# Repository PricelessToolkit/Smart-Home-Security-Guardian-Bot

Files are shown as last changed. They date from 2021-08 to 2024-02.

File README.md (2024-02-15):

# HABot

### https://youtu.be/2BBThH_CpSE

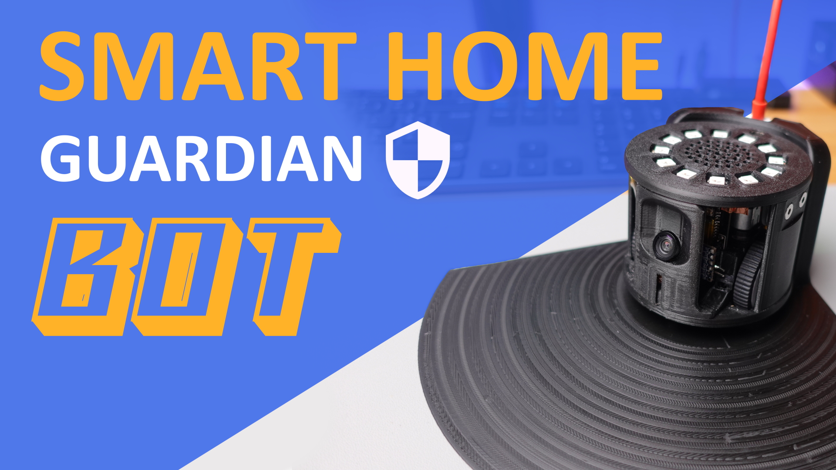
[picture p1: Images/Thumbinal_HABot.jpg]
habot (https://youtu.be/2BBThH_CpSE)


## Want to support me? Subscribe and like!

## Features

* 1: Tiny size
* 2: Wireless Charging
* 3: Voice Notifications
* 4: LED Indication
* 5: Build-in Motion sensor
* 6: Build-in Light level Sensor
* 7: MQTT Controls
* 8: Live Video stream

## Configuration Instructions
"Config_Arduino.txt" "Config_ESP32Cam.txt" "Config_Home_Assistant.txt"

## Connection diagram

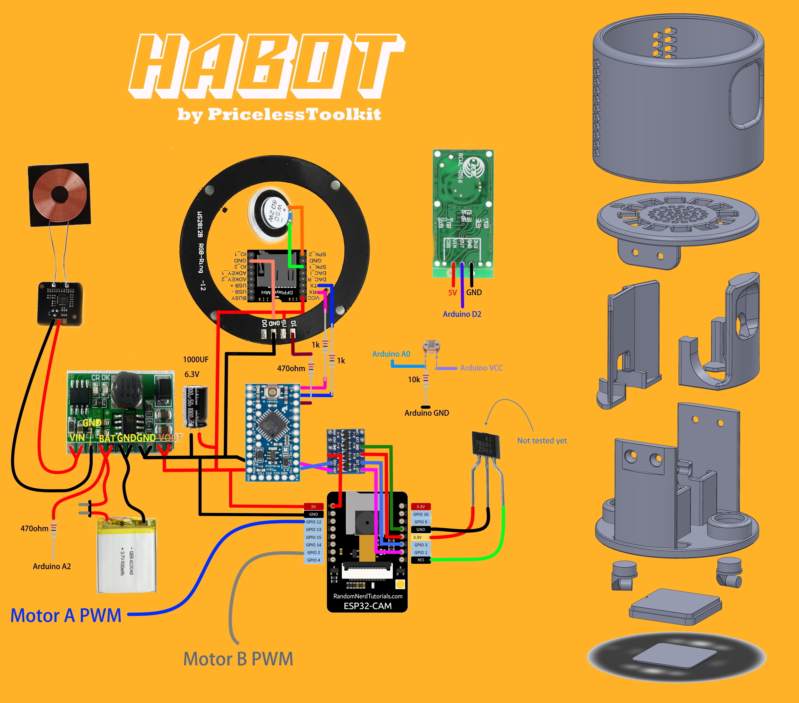
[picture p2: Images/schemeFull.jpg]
Connectiondiagram
[

## Part list

Arduino Pro Mini 5v
* 1: Speaker https://s.click.aliexpress.com/e/_AtpwE7
* 2: ESP32-CAM https://s.click.aliexpress.com/e/_AXyxo3
* 3: 160 degree OV2640 Camera https://s.click.aliexpress.com/e/_AlQi75
* 4: Wireless charger https://s.click.aliexpress.com/e/_AYQFs7
* 5: wireless charger receiver 2x2cm https://s.click.aliexpress.com/e/_API7jD
* 6: 2x Motor Single side 90deg size D https://s.click.aliexpress.com/e/_AmKxZ5
* 7: 2x Wheel https://s.click.aliexpress.com/e/_DlZWzxj
* 8: DF Player https://s.click.aliexpress.com/e/_9IVHIR
* 9: RCWL 0516 Microwave Radar Sensor https://s.click.aliexpress.com/e/_ADjEIj
* 10: LDR Light Dependent Resistor 5506 https://s.click.aliexpress.com/e/_A7hNt9
* 11: 2x chipset servo SG90  https://s.click.aliexpress.com/e/_9Qcnwr   or 2x "Servo controller tested working !" https://s.click.aliexpress.com/e/_9G644J
* 12: Charging board https://www.aliexpress.com/item/32816254080.html?spm=a2g0s.9042311.0.0.27424c4dwZKibe
* 13: Led WS2812 12xLED 5050 RGB https://s.click.aliexpress.com/e/_DBnUIml
* 14: Level SHifter https://s.click.aliexpress.com/e/_AScY1h
* 15: 1x Voltage supervisor https://s.click.aliexpress.com/e/_9HgdKX
* 16: Battery WITH PROTECTION !!!! https://s.click.aliexpress.com/e/_AXWZJD
* 17: 2 x Ball-bearing 10X15X4 mm https://s.click.aliexpress.com/e/_9G0KCn
* 18: 2 x Ball-bearing 5x10x4 https://s.click.aliexpress.com/e/_AD9iDh
* 19: 30 AWG Silicon !!! wires https://s.click.aliexpress.com/e/_Alra0B
* 20: Capacitor 6.3v 1000uf https://s.click.aliexpress.com/e/_An0GSx
* 21: Aluminum or copper self-adhesive tape
* 22: Resistors: 2 x 1K, 2 x 470R, 1x 10K
* 23: Resistor 2x SMD 0806 2.7k

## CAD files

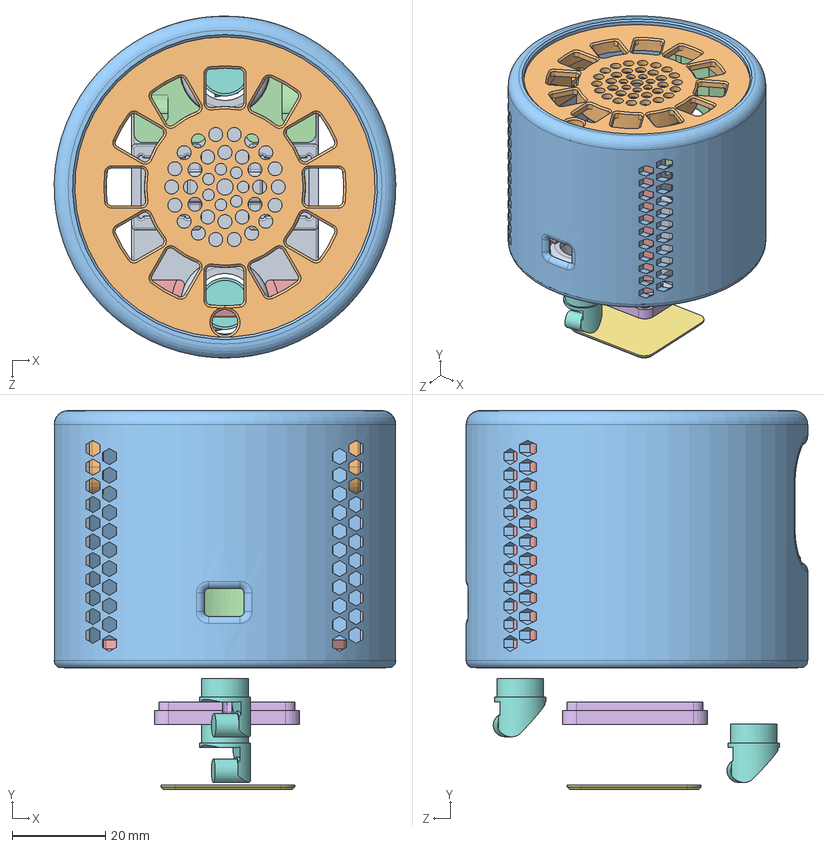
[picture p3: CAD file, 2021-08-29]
3D/SolidWorks/Assem1.SLDASM
73.2 x 81.2 x 73.2 mm
Base
Top
kash
camera holder
ArduinoHolder
WirelessChargingStand
WirelessChargingStandEndPart
bearing x 2

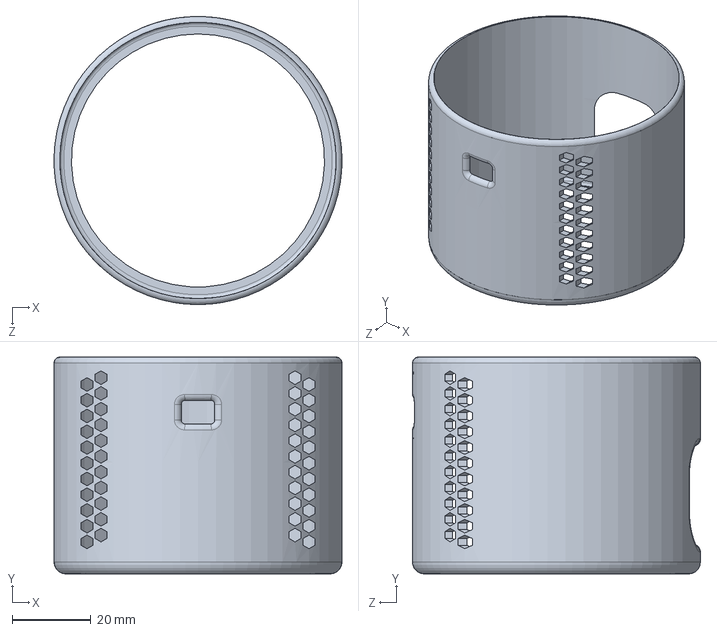
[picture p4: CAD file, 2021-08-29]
3D/SolidWorks/Cover.SLDPRT
73.2 x 55.1 x 73.2 mm

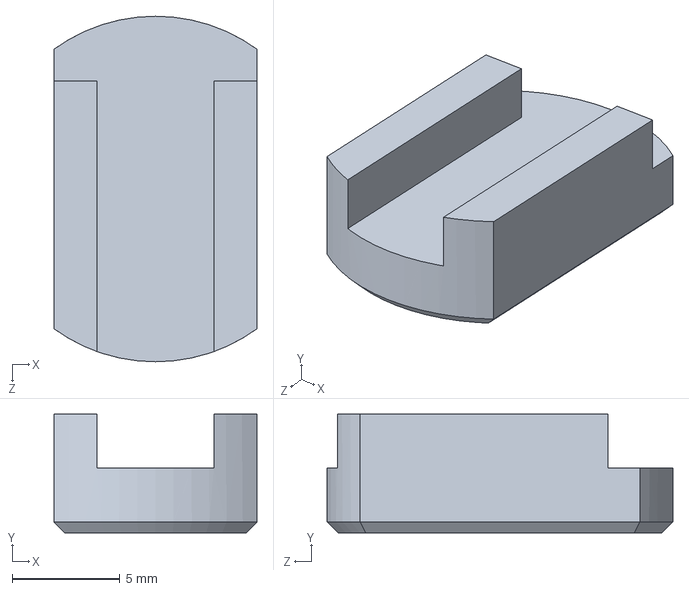
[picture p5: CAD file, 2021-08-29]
3D/SolidWorks/jumper holder.SLDPRT
9.40 x 5.50 x 16.0 mm

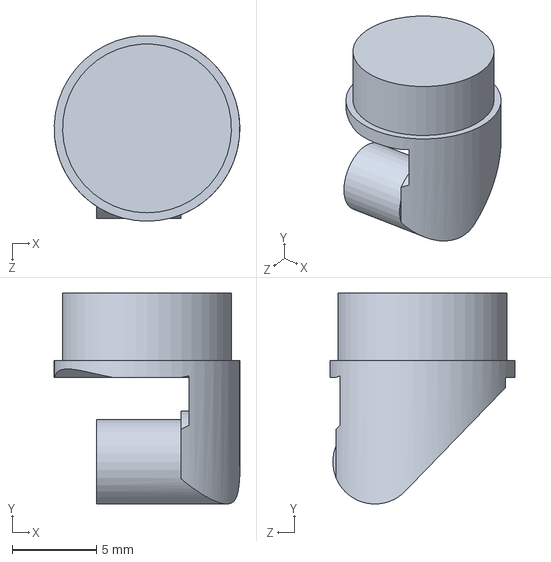
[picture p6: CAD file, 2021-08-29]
3D/SolidWorks/bearing.SLDPRT
11.0 x 12.5 x 11.0 mm

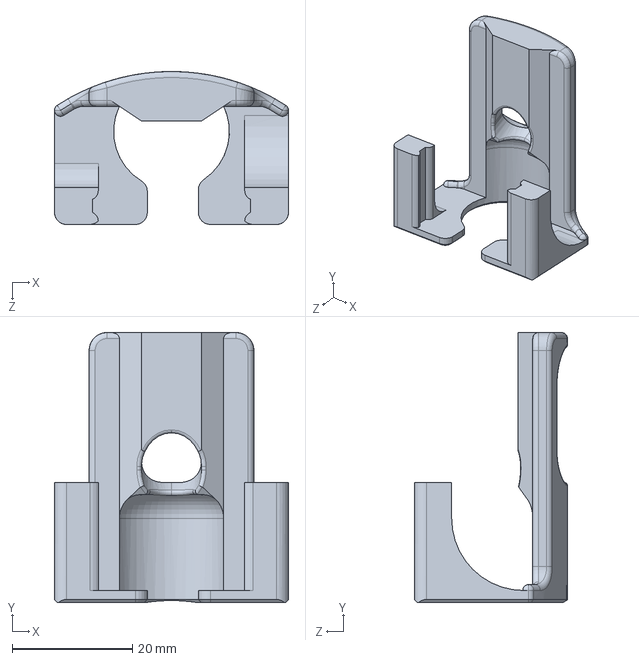
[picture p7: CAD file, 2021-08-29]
3D/SolidWorks/camera holder.SLDPRT
39.0 x 45.0 x 25.5 mm

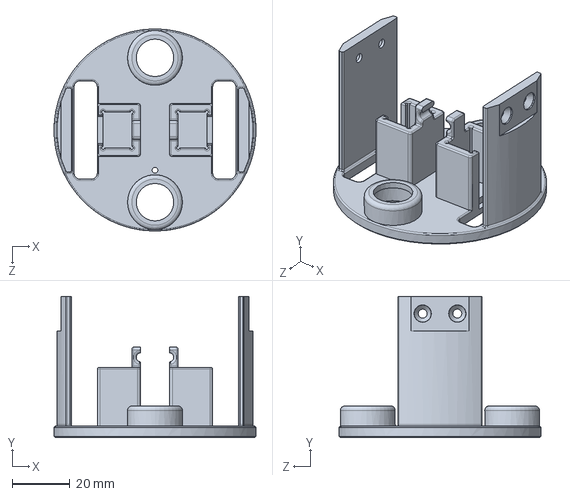
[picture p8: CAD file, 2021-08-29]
3D/SolidWorks/Base.SLDPRT
70.0 x 49.0 x 70.0 mm

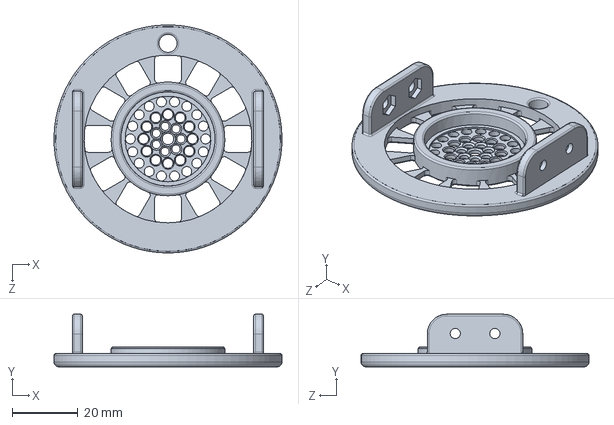
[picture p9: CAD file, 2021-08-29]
3D/SolidWorks/Top.SLDPRT
69.2 x 16.0 x 69.2 mm

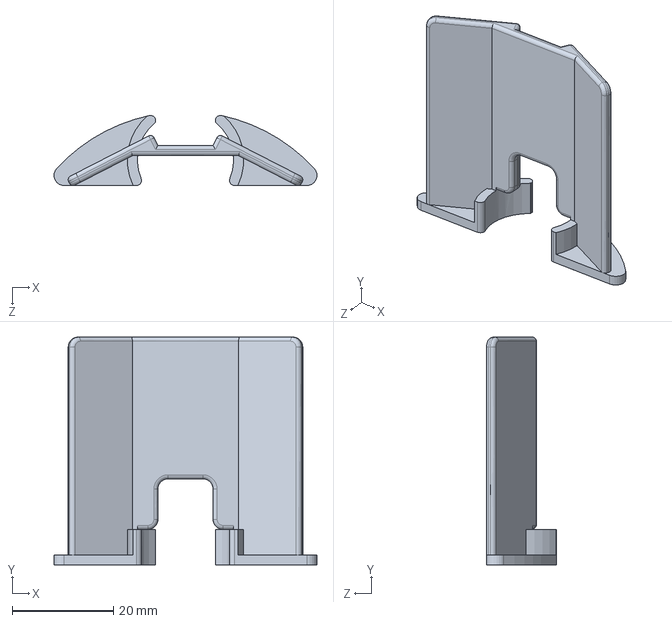
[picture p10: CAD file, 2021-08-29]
3D/SolidWorks/ArduinoHolder.SLDPRT
52.0 x 45.0 x 13.8 mm

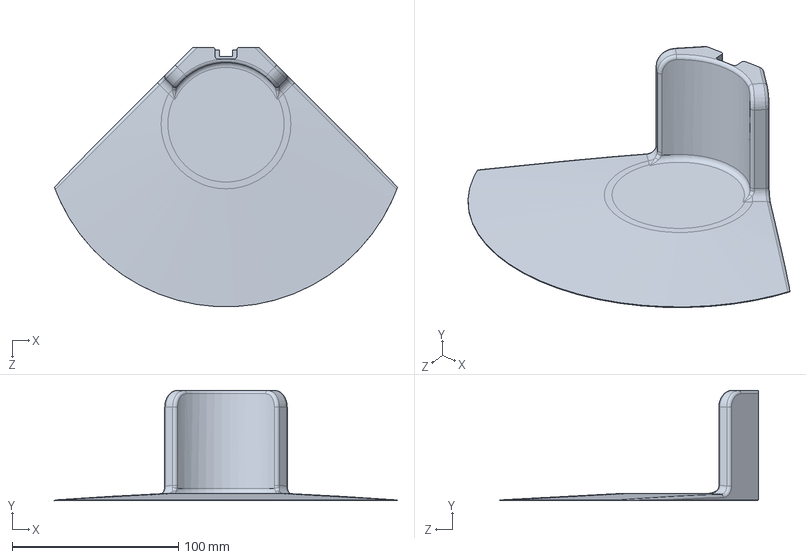
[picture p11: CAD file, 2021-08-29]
3D/SolidWorks/DockingStation.SLDPRT
206.3 x 66.3 x 155.8 mm

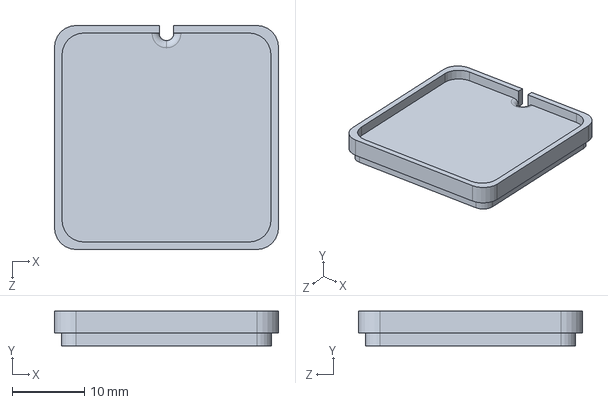
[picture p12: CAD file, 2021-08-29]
3D/SolidWorks/WirelessChargingStand.SLDPRT
31.1 x 4.80 x 31.1 mm

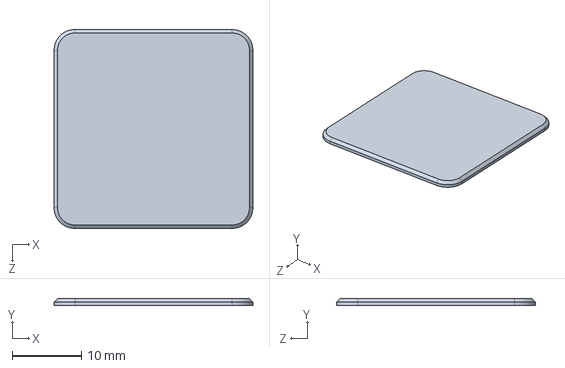
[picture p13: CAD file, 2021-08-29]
3D/SolidWorks/WirelessChargingStandEndPart.SLDPRT
28.7 x 1.00 x 28.7 mm

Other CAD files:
3D/STL/WirelessChargingStand.STL
3D/STL/WirelessChargingStandEndPart.STL
3D/STL/bearing.STL
3D/STL/jumper holder.STL

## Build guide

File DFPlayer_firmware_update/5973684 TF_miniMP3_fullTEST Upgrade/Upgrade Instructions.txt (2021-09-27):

If it is connected to ardunio, please use the ino in the folder to test.

1. The files in the TF card should be cleared first. The format is: FAT32

2. Copy the update.ufw (the name and suffix cannot be changed) to the card, don¡¯t change the name, don¡¯t put it in the subdirectory, put it in the root directory

3. Plug in the TF card and power on, and you will hear a beep, indicating that the upgrade is complete

4. Delete the upgrade file in the card and put back the previous track

If it is connected to ardunio, please use the ino in the folder to test

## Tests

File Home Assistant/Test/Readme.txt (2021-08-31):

Thys is for test "this code doesn't work"

And who know how to program like a Jedi, look at the test folder, and if u can please contribute to the project, It will be wonderful.

I think problem is here 

  <script src="jquery-3.5.0.js"></script>
  <script src="mqttws31.min.js"></script>
  <script src="app.js"></script>

i need to do something like this

import "jquery-3.5.0.js?module";
import "mqttws31.min.js?module";
import "app.js?module";

but UI give me an error

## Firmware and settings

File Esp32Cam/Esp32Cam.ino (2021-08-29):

#include <ArduinoJson.h>
#include "esp_camera.h"
#include "esp_timer.h"
#include "img_converters.h"
#include "fb_gfx.h"
#include "soc/soc.h" //disable brownout problems
#include "soc/rtc_cntl_reg.h"  //disable brownout problems
#include "esp_http_server.h"
#include <WiFi.h>
#include <PubSubClient.h>
#include "Arduino.h"
#define LED_BUILTIN 4


const int fwdPin = 2;  
const int turnPin = 12;  

// Arduino like analogWrite
// value has to be between 0 and valueMax
void fwdAnalogWrite(uint8_t channel, uint32_t value, uint32_t valueMax = 2000) {
  // calculate duty, 8191 from 2 ^ 13 - 1
  uint32_t duty = (8191 / valueMax) * min(value, valueMax);
  ledcWrite(channel, duty);
}
void steeringAnalogWrite(uint8_t channel, uint32_t value, uint32_t valueMax = 2000) {
  // calculate duty, 8191 from 2 ^ 13 - 1
  uint32_t duty = (8191 / valueMax) * min(value, valueMax);
  ledcWrite(channel, duty);
}

const char* ssid = "Your_wifiname";
const char* password = "Your_password";
const char* mqtt_username = "Your_mqtt_username";
const char* mqtt_password = "Your_mqtt_password";
const char* mqtt_server = "Your_mqtt/homeassistant server IP";
const int mqtt_port = 1883;

WiFiClient espClient;
PubSubClient client(espClient);

void setup_wifi() {
  delay(10);
  // We start by connecting to a WiFi network

  WiFi.begin(ssid, password);

  while (WiFi.status() != WL_CONNECTED) {
	  
    steeringAnalogWrite(2, 0); // STOP when WIFI is not connected
    steeringAnalogWrite(4, 0); // STOP when WIFI is not connected
	Serial.println(1001); // Searching WIFI
    delay(500);
    
  }

  Serial.println(1002); // WiFi Is Connected


    // Start streaming web server
  startCameraServer();
}




#define PART_BOUNDARY "123456789000000000000987654321"

// This project was tested with the AI Thinker Model, M5STACK PSRAM Model and M5STACK WITHOUT PSRAM

  #define PWDN_GPIO_NUM     32
  #define RESET_GPIO_NUM    -1
  #define XCLK_GPIO_NUM      0
  #define SIOD_GPIO_NUM     26
  #define SIOC_GPIO_NUM     27
  
  #define Y9_GPIO_NUM       35
  #define Y8_GPIO_NUM       34
  #define Y7_GPIO_NUM       39
  #define Y6_GPIO_NUM       36
  #define Y5_GPIO_NUM       21
  #define Y4_GPIO_NUM       19
  #define Y3_GPIO_NUM       18
  #define Y2_GPIO_NUM        5
  #define VSYNC_GPIO_NUM    25
  #define HREF_GPIO_NUM     23
  #define PCLK_GPIO_NUM     22


static const char* _STREAM_CONTENT_TYPE = "multipart/x-mixed-replace;boundary=" PART_BOUNDARY;
static const char* _STREAM_BOUNDARY = "\r\n--" PART_BOUNDARY "\r\n";
static const char* _STREAM_PART = "Content-Type: image/jpeg\r\nContent-Length: %u\r\n\r\n";

httpd_handle_t stream_httpd = NULL;

static esp_err_t stream_handler(httpd_req_t *req){
  camera_fb_t * fb = NULL;
  esp_err_t res = ESP_OK;
  size_t _jpg_buf_len = 0;
  uint8_t * _jpg_buf = NULL;
  char * part_buf[64];

  res = httpd_resp_set_type(req, _STREAM_CONTENT_TYPE);
  if(res != ESP_OK){
    return res;
  }

  while(true){
    fb = esp_camera_fb_get();
    if (!fb) {
      Serial.println("Camera capture failed");
      res = ESP_FAIL;
    } else {
      if(fb->width > 400){
        if(fb->format != PIXFORMAT_JPEG){
          bool jpeg_converted = frame2jpg(fb, 80, &_jpg_buf, &_jpg_buf_len);
          esp_camera_fb_return(fb);
          fb = NULL;
          if(!jpeg_converted){
            Serial.println("JPEG compression failed");
            res = ESP_FAIL;
          }
        } else {
          _jpg_buf_len = fb->len;
          _jpg_buf = fb->buf;
        }
      }
    }
    if(res == ESP_OK){
      size_t hlen = snprintf((char *)part_buf, 64, _STREAM_PART, _jpg_buf_len);
      res = httpd_resp_send_chunk(req, (const char *)part_buf, hlen);
    }
    if(res == ESP_OK){
      res = httpd_resp_send_chunk(req, (const char *)_jpg_buf, _jpg_buf_len);
    }
    if(res == ESP_OK){
      res = httpd_resp_send_chunk(req, _STREAM_BOUNDARY, strlen(_STREAM_BOUNDARY));
    }
    if(fb){
      esp_camera_fb_return(fb);
      fb = NULL;
      _jpg_buf = NULL;
    } else if(_jpg_buf){
      free(_jpg_buf);
      _jpg_buf = NULL;
    }
    if(res != ESP_OK){
      break;
    }
    //Serial.printf("MJPG: %uB\n",(uint32_t)(_jpg_buf_len));
  }
  return res;
}


void startCameraServer(){
  httpd_config_t config = HTTPD_DEFAULT_CONFIG();
  config.server_port = 80;

  httpd_uri_t index_uri = {
    .uri       = "/",
    .method    = HTTP_GET,
    .handler   = stream_handler,
    .user_ctx  = NULL
  };
  
  //Serial.printf("Starting web server on port: '%d'\n", config.server_port);
  if (httpd_start(&stream_httpd, &config) == ESP_OK) {
    httpd_register_uri_handler(stream_httpd, &index_uri);
  }
}

void reconnect() {
  while (!client.connected()) {

    Serial.println(1003); // Conectioon Faild
    steeringAnalogWrite(2, 0); // STOP when MQTT is not connected
    steeringAnalogWrite(4, 0); // STOP when MQTT is not connected
 
    // Create a random client ID
    String clientId = "HABot";

    // Attempt to connect
    if (client.connect("HABot", mqtt_username, mqtt_password)) {

      client.subscribe("HABot/Commands/Steering");
      client.subscribe("HABot/Commands/Data");
      Serial.println(1004); // MQTT Connected


      
    }
    else
    {
      // Wait 0.1 seconds before retrying
      delay(100);
    }
  }
}

void MQTTCallback(char* topic, byte* payload, unsigned int length) {
  String Command = "";

  for (int i = 0; i < length; i++) {
    Command = Command + (char)payload[i];
  }  

  Serial.println(Command); // Send all Data to arduino
  
  int data = Command.toInt();
  
  if(strcmp(topic, "HABot/Commands/Steering") == 0)
  {
	if (Command == "right")
	{
	steeringAnalogWrite(4, 1120);
	steeringAnalogWrite(2, 1220);
	}
   


	if (Command == "left")
	{
	steeringAnalogWrite(2, 1150);
	steeringAnalogWrite(4, 1200);
	}


   if (Command == "forward")
    {
    steeringAnalogWrite(2, 1022);
    steeringAnalogWrite(4, 1000);
    }

   if (Command == "backward")
    {
    steeringAnalogWrite(2, 1240);
    steeringAnalogWrite(4, 1218);
    }

    if (Command == "stop")
    {
    steeringAnalogWrite(2, 0);
    steeringAnalogWrite(4, 0);
    }
    
  }

}


void DeserializAndPub(){
  
     StaticJsonDocument<128> doc;
     while (Serial.available() > 0)
    {
    DeserializationError error = deserializeJson(doc, Serial);

    if (error) {
    Serial.print(F("deserializeJson() failed: "));
    Serial.println(error.f_str());
    return;
    }

    const char* sensors = doc["sensors"]; // "HaBot"
    const char* Light = doc["Light"]; // "210"
    const char* Bat = doc["Bat"]; // "10"
    const char* Motion = doc["Motion"]; // "HIGH"
    char buffer[128];
    size_t n = serializeJson(doc, buffer);
    client.publish("HABot/sensors", buffer, n);
    client.endPublish();


        }
    

    return;
}

void setup(){



  WRITE_PERI_REG(RTC_CNTL_BROWN_OUT_REG, 0); //disable brownout detector
  Serial.begin(115200);
  pinMode (LED_BUILTIN, OUTPUT);
  pinMode (LED_BUILTIN, LOW);


  // forward motor PWM
  ledcSetup(2, 50, 16); //channel, freq, resolution
  ledcAttachPin(fwdPin, 2); // pin, channel
 
  // steering servo PWM
  ledcSetup(4, 50, 16); //channel, freq, resolution
  ledcAttachPin(turnPin, 4); // pin, channel 

  setup_wifi();
  client.setServer(mqtt_server, mqtt_port);
  reconnect();
  client.setCallback(MQTTCallback);  

    camera_config_t config;
  config.ledc_channel = LEDC_CHANNEL_0;
  config.ledc_timer = LEDC_TIMER_0;
  config.pin_d0 = Y2_GPIO_NUM;
  config.pin_d1 = Y3_GPIO_NUM;
  config.pin_d2 = Y4_GPIO_NUM;
  config.pin_d3 = Y5_GPIO_NUM;
  config.pin_d4 = Y6_GPIO_NUM;
  config.pin_d5 = Y7_GPIO_NUM;
  config.pin_d6 = Y8_GPIO_NUM;
  config.pin_d7 = Y9_GPIO_NUM;
  config.pin_xclk = XCLK_GPIO_NUM;
  config.pin_pclk = PCLK_GPIO_NUM;
  config.pin_vsync = VSYNC_GPIO_NUM;
  config.pin_href = HREF_GPIO_NUM;
  config.pin_sscb_sda = SIOD_GPIO_NUM;
  config.pin_sscb_scl = SIOC_GPIO_NUM;
  config.pin_pwdn = PWDN_GPIO_NUM;
  config.pin_reset = RESET_GPIO_NUM;
  config.xclk_freq_hz = 20000000;
  config.pixel_format = PIXFORMAT_JPEG; 
  
  if(psramFound()){
    config.frame_size = FRAMESIZE_VGA;
    config.jpeg_quality = 25;
    config.fb_count = 2;
  } else {
    config.frame_size = FRAMESIZE_VGA;
    config.jpeg_quality = 25;
    config.fb_count = 1;
  }
  
  // Camera init
  esp_err_t err = esp_camera_init(&config);
  if (err != ESP_OK) {
    Serial.printf("Camera init failed with error 0x%x", err);
    return;
  }
  
}

void loop(){
      if (!client.connected()) 
        {
            reconnect();
        }
        
    DeserializAndPub();

  client.loop();
}

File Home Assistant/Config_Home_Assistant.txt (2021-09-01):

MQTT Information


********************** DRIVING ******************************
 TOPIC: "HABot/Commands/Steering"

 "HABot/Commands/Steering"
  Values = "right", "left", "forward", "backward", "stop".



*********************** Control of periphery ******************

 TOPIC:  "HABot/Commands/Data" 

---------------DFPlayer Control ---------------------------

   Copy mp3 folder into SD card folder name should be mp3 and file names 003,004,005...

   if command starts with "mp3"  mp3xxxxxx
   Values = "mp3XXAAA"  ( XX is Volium level 2 digits 00-30 ) (AAA is mp3 file name 001,002,003).


 ---------- LED Controll -------------------

   if commands = 4 digits
   Values = "1001",1002...... 



*********************** Telemetry ************************

BOT Publish Sensor Values in json.

 TOPIC: "HABot/sensors"
 Value = {"sensors": "HaBot","Light": 93,"Bat": 95,"Motion": 0}

***************************************************************







HOME ASSISTANT Configuration
*********************************************************************************************

1. In habot folder, file "app.js"  open it and change Your_HA_IP, Your_MQTT_Username, Your_MQTT_Password
2. Copy habot folder to "config\www\custom_lovelace"  WARNING www folder is publicly avaliable !!!! "There is no access control" Use VPN or WireGuard (Your Phone > VPN Client > INTERNET > VPN Server > Home assistant
3. In HOME ASSISTANT create sensor "battery, Motion, Light Level".  "habot.yaml" file includeed 



sensor:
 - platform: mqtt
   name: "HABot Battery"
   state_topic: "HABot/sensors"
   json_attributes_topic: "HABot/sensors"
   unit_of_measurement: '%'
   value_template: '{{value_json.Bat}}'
 - platform: mqtt
   name: "HABot Light Level"
   state_topic: "HABot/sensors"
   json_attributes_topic: "HABot/sensors"
   unit_of_measurement: '%'
   value_template: '{{value_json.Light}}'
 - platform: mqtt
   name: "HABot Motion Sensor"
   state_topic: "HABot/sensors"
   json_attributes_topic: "HABot/sensors"
   unit_of_measurement: ''
   value_template: '{{value_json.Motion}}'





For control use UI vertical stock EXAMPLE ALL in ONE

**********************************

type: vertical-stack
cards:
  - type: picture
    image: http://YOUR_HABot_IP/
    tap_action:
      action: none
    hold_action:
      action: none
  - type: glance
    entities:
      - entity: sun.sun
        name: ERROR
        tap_action:
          navigation_path: none
          url_path: none
          action: call-service
          service: mqtt.publish
          service_data:
            topic: HABot/Commands/Data
            payload: mp320003
      - entity: sun.sun
        name: I see you
        tap_action:
          navigation_path: none
          url_path: none
          action: call-service
          service: mqtt.publish
          service_data:
            topic: HABot/Commands/Data
            payload: mp320004
      - entity: sun.sun
        name: POLICE
        tap_action:
          navigation_path: none
          url_path: none
          action: call-service
          service: mqtt.publish
          service_data:
            topic: HABot/Commands/Data
            payload: mp320006
      - entity: sun.sun
        name: MDF
        tap_action:
          navigation_path: none
          url_path: none
          action: call-service
          service: mqtt.publish
          service_data:
            topic: HABot/Commands/Data
            payload: mp320007
      - entity: sun.sun
        name: Notify
        tap_action:
          navigation_path: none
          url_path: none
          action: call-service
          service: mqtt.publish
          service_data:
            topic: HABot/Commands/Data
            payload: mp320008
      - entity: sun.sun
        name: Color 1
        tap_action:
          navigation_path: none
          url_path: none
          action: call-service
          service: mqtt.publish
          service_data:
            topic: HABot/Commands/Data
            payload: 1001
      - entity: sun.sun
        name: Color 2
        tap_action:
          navigation_path: none
          url_path: none
          action: call-service
          service: mqtt.publish
          service_data:
            topic: HABot/Commands/Data
            payload: 1002
      - entity: sun.sun
        name: Color 3
        tap_action:
          navigation_path: none
          url_path: none
          action: call-service
          service: mqtt.publish
          service_data:
            topic: HABot/Commands/Data
            payload: 1003
      - entity: sun.sun
        name: Color 4
        tap_action:
          navigation_path: none
          url_path: none
          action: call-service
          service: mqtt.publish
          service_data:
            topic: HABot/Commands/Data
            payload: 1004
    show_icon: false
    show_state: false
    state_color: false
    show_name: true
  - type: iframe
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

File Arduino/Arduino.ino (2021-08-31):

#include <ArduinoJson.h>
#include <DFPlayer_Mini_Mp3.h>

#if !defined(UBRR1H)
#include <SoftwareSerial.h>
SoftwareSerial mySerial(8, 9); // RX, TX
#endif

#include <Adafruit_NeoPixel.h>
Adafruit_NeoPixel leds = Adafruit_NeoPixel(12, 7, NEO_GRB + NEO_KHZ800);

String inData;
String Message;
int Commands;
String Volume;
String Track;
int vol;
int tr;

int period10ms = 10;
int period100ms = 100;
int period500ms = 500;
int period1000ms = 1000;
int period2000ms = 2000;
unsigned long time_now = 0;

int MotionPin = 2;
int MotionState = 0;

StaticJsonDocument<64> doc;

void setup(){


  //analogReference(INTERNAL);  
  pinMode(MotionPin, INPUT);
  
  Serial.begin(115200);
  mySerial.begin (9600);
  
  mp3_set_serial (mySerial);	//set softwareSerial for DFPlayer-mini mp3 module 
  delay(10);  //wait 2ms for mp3 module to set volume
  mp3_set_volume (20);
  delay(20);

/*
   mp3_play ();    //start play
   mp3_play (5);  //play "mp3/0005.mp3"
   mp3_next ();   //play next 
   mp3_prev ();   //play previous
   mp3_set_volume (uint16_t volume);  //0~30
   mp3_set_EQ (); //0~5
   mp3_pause ();
   mp3_stop ();
   void mp3_get_state ();   //send get state command
   void mp3_get_volume (); 
   void mp3_get_u_sum (); 
   void mp3_get_tf_sum (); 
   void mp3_get_flash_sum (); 
   void mp3_get_tf_current (); 
   void mp3_get_u_current (); 
   void mp3_get_flash_current (); 
   void mp3_single_loop (boolean state);  //set single loop 
   void mp3_DAC (boolean state); 
   void mp3_random_play (); 
 */
    
  leds.begin();
  leds.setBrightness(50); // 1-255
  leds.show(); // Initialize all pixels to 'off'
  
}



void loop(){
   int Batt = map(analogRead(A2), 650, 867, 0, 100); // (analogRead(A2), MIN, MAX, 0, 100)
   // Serial.println(analogRead(A2); // Take note of min and max values when the battery is 3.2v and 4.2v. And write these values in line 77  MIN-MAX
   int Light = map(analogRead(A0), 1, 1024, 0, 100);
   MotionState = digitalRead(MotionPin);
   
   doc["sensors0"] = "HaBot";
   doc["Light"] = Light;
   doc["Bat"] = Batt;
   doc["Motion"] = MotionState;

  if(millis() >= time_now + period2000ms){
    time_now += period2000ms;
    serializeJson(doc, Serial);
  }

    while (Serial.available() > 0)
    {
        char recieved = Serial.read();
        inData += recieved; 

        // Process message when new line character is recieved
        if (recieved == '\n')
        {

          Message = inData.substring(0, inData.length() - 1); // Delet last character "\n"
          Commands = Message.toInt(); // Convert to int
  



          switch (Commands) {
            case 1001: // Searching WiFi
                 for(uint16_t i=0; i<leds.numPixels(); ) {
                    leds.setPixelColor(i, 255, 128, 0);
                    leds.show();

                  if(millis() >= time_now + period100ms){
                    time_now += period100ms;
                    leds.clear();
                    leds.show();
                    i++;
                     
                    }
                }
              break;
            case 1002: // WiFi Connected

                 for(uint16_t i=0; i<leds.numPixels(); ) {
                    leds.setPixelColor(i, 147, 228, 28);
                    leds.show();

                  if(millis() >= time_now + period10ms){
                    time_now += period10ms;
                    leds.clear();
                    leds.show();
                    i++;
                     
                    }
                }
              break;
            case 1003: // MQTT Connection Failed

                 for(uint16_t i=0; i<leds.numPixels(); ) {
                    leds.setPixelColor(i, 255, 0, 0);
                    leds.show();

                  if(millis() >= time_now + period100ms){
                    time_now += period100ms;
                    leds.clear();
                    leds.show();
                    i++;
                     
                    }
                }
              break;
            case 1004: // MQTT Connected
                    
                 for(uint16_t i=0; i<leds.numPixels(); ) {
                    leds.setPixelColor(i, 0, 31, 255);
                    leds.show();

                  if(millis() >= time_now + period10ms){
                    time_now += period10ms;
                    leds.clear();
                    leds.show();
                    i++;
                     
                    }
                }
              break;
            default:
              break;
          }
          
           // mp3251   volume is 25 Track numper 1
          if(Message.substring(0,3)== "mp3"){
            Volume = Message.substring(3,5);
            Track = Message.substring(5,8);
            vol = Volume.toInt();
            tr = Track.toInt();
            mp3_set_volume (vol);
            delay(50);
            mp3_play (tr);
            
          }
          
            inData = ""; // Clear recieved buffer
        }

       time_now = millis();
       

    }


}

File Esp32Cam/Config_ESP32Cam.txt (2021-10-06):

Code line: 32 - 37 Login information "Your_wifiname, Your_password, Your_mqtt_username, Your_mqtt_password, Your_mqtt/homeassistant server IP"
Code line: 214 - 245 Stearing Calibration You need to tweak PWM values.

**************************************************************************

Since the resistors on servo controllers  have an "Value error %"
You need to tweak settings ( PWM values "xxxx") so that the left and right mator
spin at the same speed for "Forward" and "backward" and of course in the right direction. . For "LEFT, RIGHT" opposite directions and slower speed.  



   if (Command == "forward")
    {
    steeringAnalogWrite(2, xxxx);
    steeringAnalogWrite(4, xxxx);
    }

   if (Command == "backward")
    {
    steeringAnalogWrite(2, xxxx);
    steeringAnalogWrite(4, xxxx);
    }

    if (Command == "stop")
    {
    steeringAnalogWrite(2, 0);
    steeringAnalogWrite(4, 0);
    }


-------------------------------------------- For  ESC Version from Ali approximate PWM values------------------------------------

https://www.aliexpress.com/item/1005001703606384.html?spm=a2g0o.cart.0.0.17523c00rWJPYe&mp=1



if (Command == "right")
		{
		steeringAnalogWrite(4, 1260);
		steeringAnalogWrite(2, 1160);
    //Serial.println("ok");
		}
   


	 if (Command == "left")
		{
		steeringAnalogWrite(2, 1260);
		steeringAnalogWrite(4, 1160);
		}


   if (Command == "forward")
    {
    steeringAnalogWrite(2, 1500);
    steeringAnalogWrite(4, 900);
    }

   if (Command == "backward")
    {
    steeringAnalogWrite(2, 1160);
    steeringAnalogWrite(4, 1260);
    }

    if (Command == "stop")
    {
    steeringAnalogWrite(2, 0);
    steeringAnalogWrite(4, 0);
    }

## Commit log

2021-08-29 File Names
    [Config_Arduino.txt, Config_ESP32Cam.txt, Config_Home_Assistant.txt]
2021-08-31 Update Config_Home_Assistant.txt
    UI Config
    [Config_Home_Assistant.txt]
2021-09-01 Yaml file Name
    [Config_Home_Assistant.txt]
2021-10-05 servo controller
    Servo controller Tested working!
2023-06-02 added device_class
